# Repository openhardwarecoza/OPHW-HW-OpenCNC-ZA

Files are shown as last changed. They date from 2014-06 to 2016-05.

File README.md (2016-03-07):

# OPHW-HW-OpenCNC-ZA

Release link for Version 2: https://plus.google.com/+PetervanderWalt/posts/GEEHTLkx1Rs

Youtube Playlist: (Mostly the older V1 videos): https://www.youtube.com/watch?v=i0t9h2HhJ-g&list=PL1JTb6-HQgOwBOFXhe4r-cTgKN7O4TTUV
(Note: The V2 is a much more rigit beast than the V1 was - switching to OpenBuilds V-Slot made a massive difference over 12mm stainless shafts that V1 used)

Photos of the machines: https://github.com/openhardwarecoza/OPHW-HW-OpenCNC-ZA/tree/master/Photos

###Groupbuy of V2 Frames 

(March 2016:  $300 if we get 10 people): https://plus.google.com/112804366993013346159/posts/UJpufFbkruB

## New Version: V2
OPHW-HW-OpenCNC-SMW
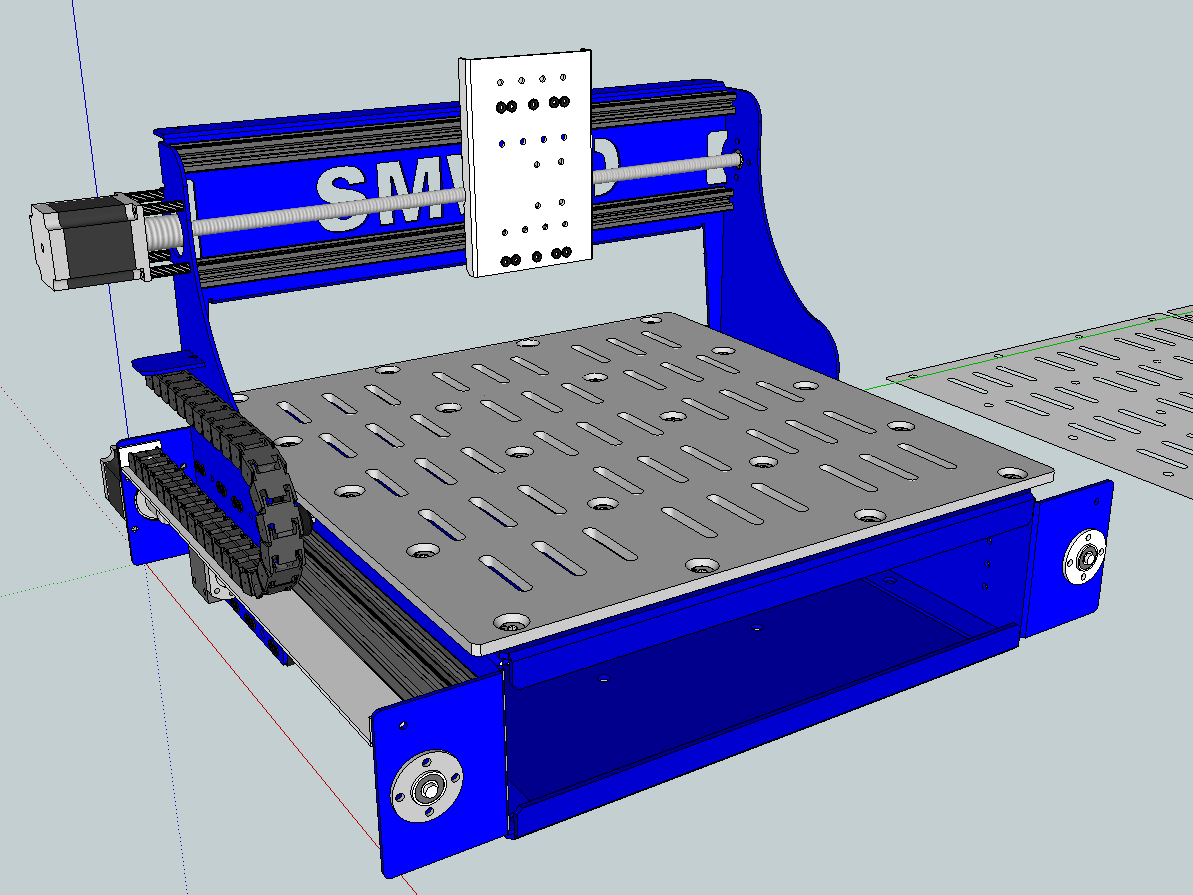
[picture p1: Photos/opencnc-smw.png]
OpenCNC-SMW


## Legacy Version:  V1
OPHW-HW-OpenCNC-ZA
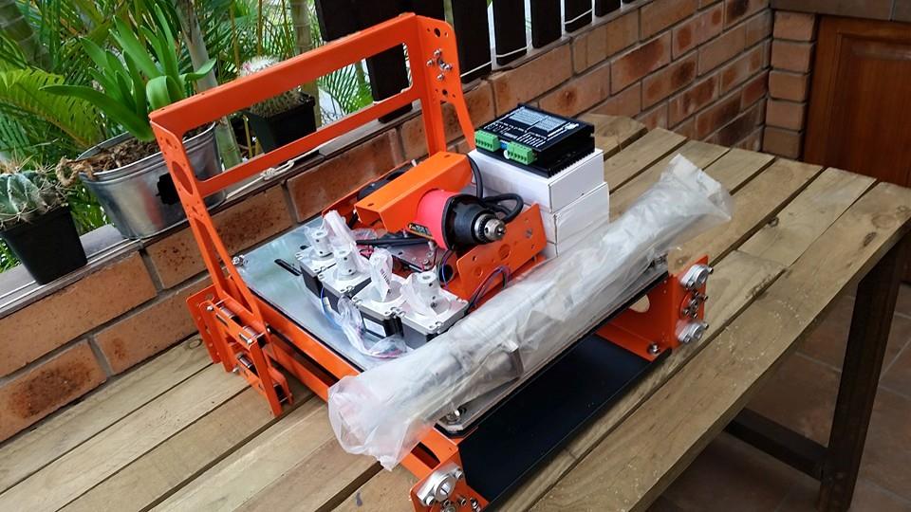
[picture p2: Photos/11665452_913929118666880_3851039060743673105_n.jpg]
OpenCNC-ZA


74 x Photos build Album of V1: https://plus.google.com/+PetervanderWalt/posts/8sR3STWhrXN

Specs V1: 200x300mm work area, 12mm ballscrews all round, 12mm stainless steel shafts,

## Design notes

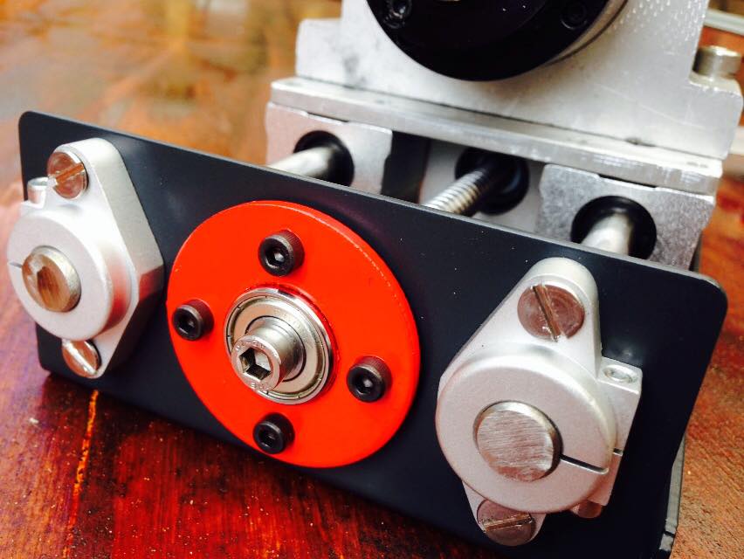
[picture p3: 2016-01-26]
Photos/10593230_783649345028192_9119679206650763691_n.jpg

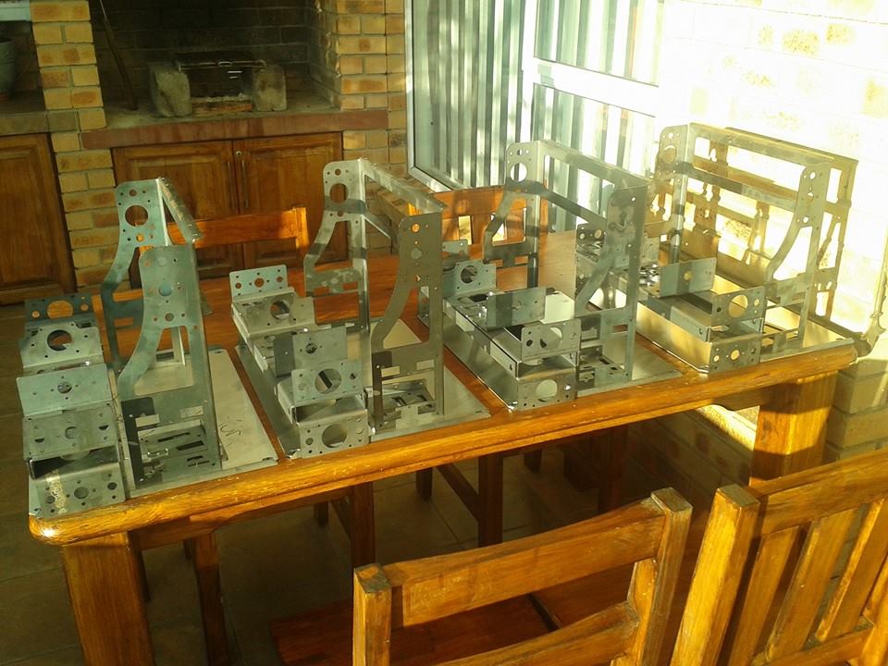
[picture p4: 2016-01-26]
Photos/537115_678176878908773_2035238081_n.jpg

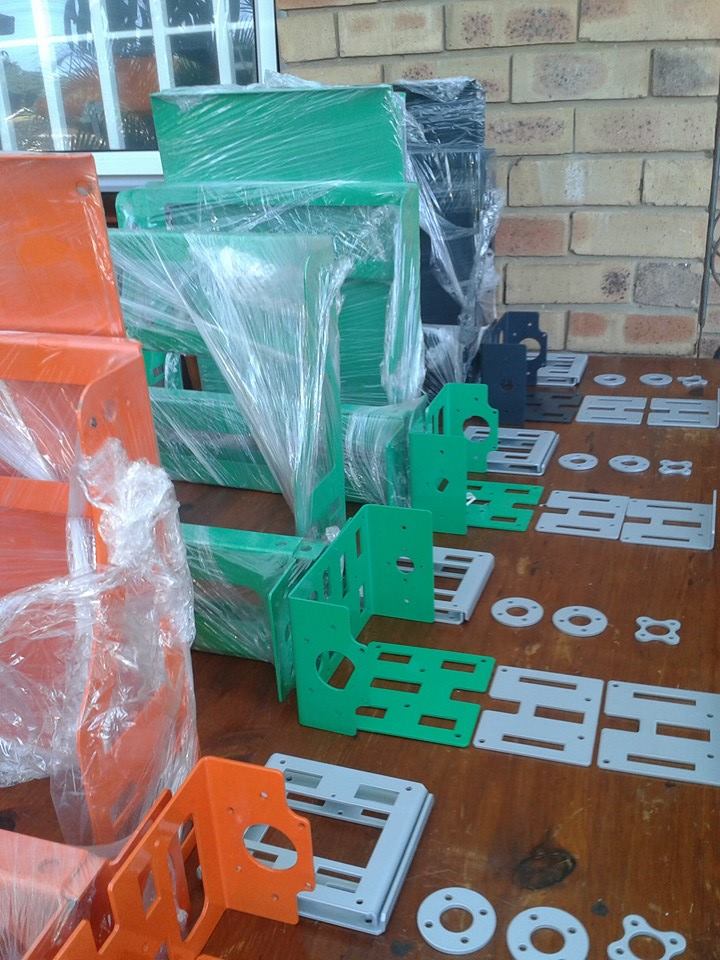
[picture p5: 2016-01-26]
Photos/10007480_681862631873531_1897662941_n.jpg

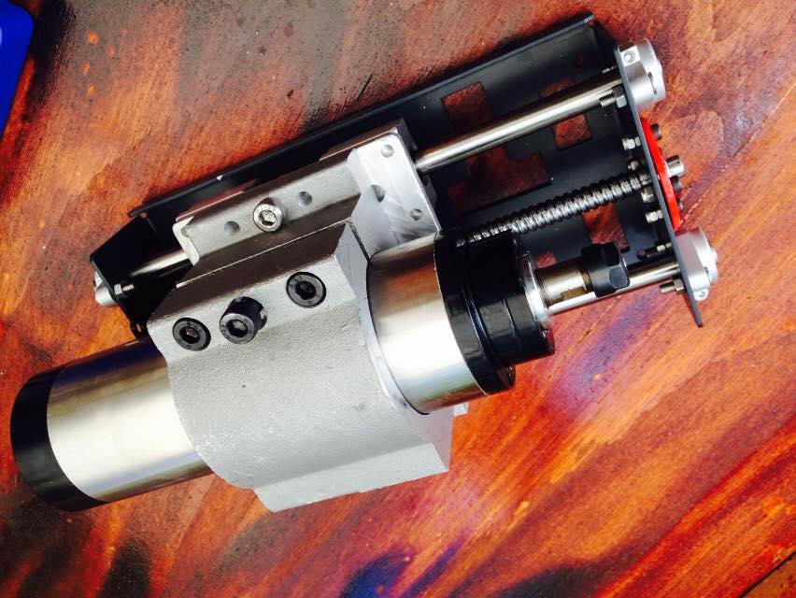
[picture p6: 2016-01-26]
Photos/10730114_783649301694863_8155415779819512405_n.jpg

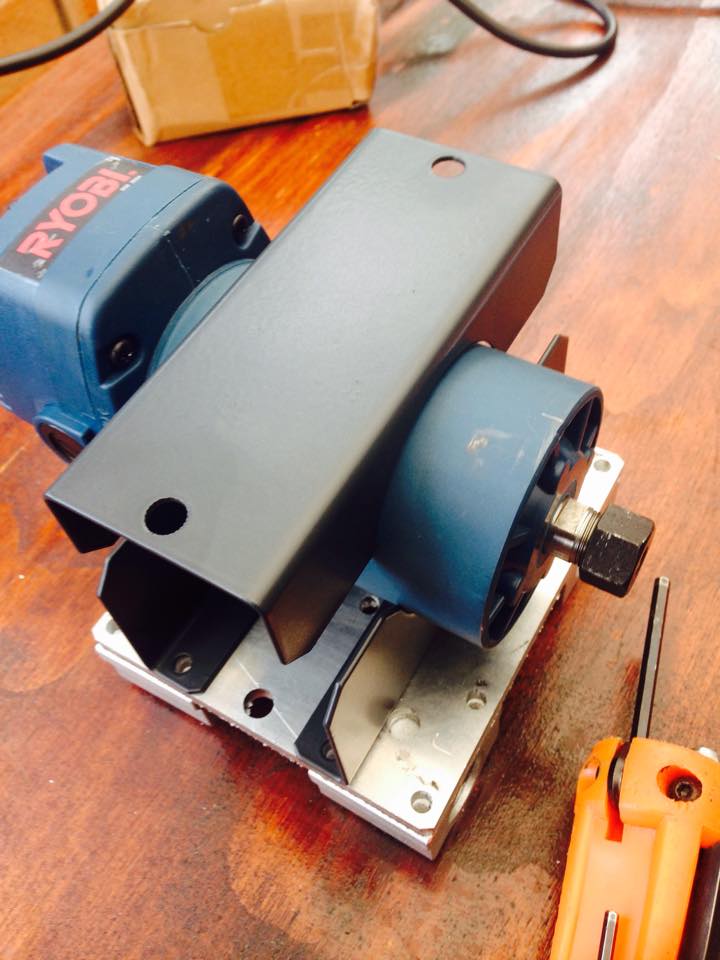
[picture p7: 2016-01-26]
Photos/1622716_788742607852199_260670169807607488_n.jpg

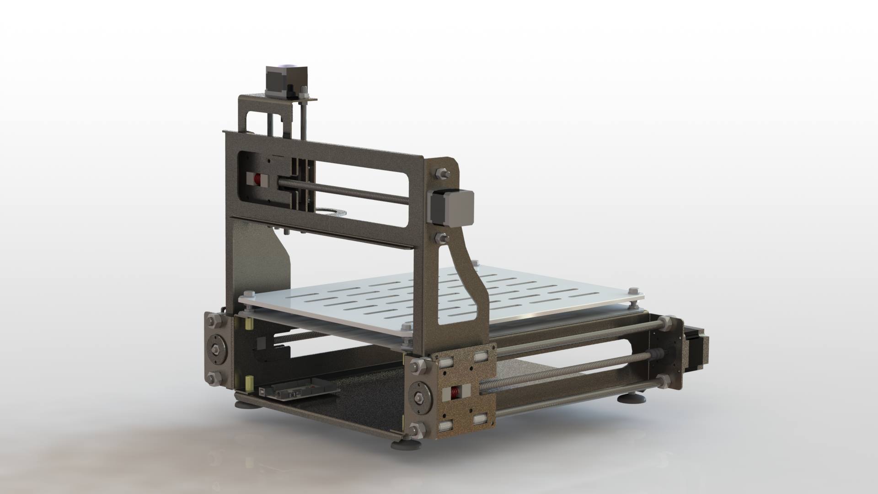
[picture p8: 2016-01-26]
Photos/1798963_653309631395498_944965548_o.jpg

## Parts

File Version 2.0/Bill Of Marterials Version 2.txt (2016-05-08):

(From OpenBuilds)
2 qty 20x80 VSLOT 500mm Length (Y Rails)
2 qty 20x20 VSLOT Between 500 and 530mm long - not critical (X Rails)
10 qty Openbuilds Spacer Blocks (http://openbuildspartstore.com/spacer-block/)
22 qty  OpenBuilds V-Wheels (Extreme PC would be even stiffer) http://openbuildspartstore.com/solid-v-wheel-kit/
11 qty 1/4 Eccentric Spacers http://openbuildspartstore.com/eccentric-spacer/
11 qty 1/4 Aluminum Spacers http://openbuildspartstore.com/aluminum-spacers/
12 qty 35mm Aluminum Spacers (Space motors out so couplers doesnt interfere inside moveable area of carriages) http://openbuildspartstore.com/aluminum-spacers/

(Z Axis)
1 x complete C-Beam Kit 250mm (Or own design) for openbuilds

(Leadscrews) (Note discussion on length on google plus)
3 qty 1204 Ballnut
3 qty 1204 Ballnut Mounting Block (like http://s.click.aliexpress.com/e/QvznIYRvZ)
2 qty Ballscrew 505mm between insides (So total length = 505mm + turned down section for shaft coupler + turned down and threaded section for restraining)
1 qty Ballscrew 530mm between insides  (So total length = 530mm + turned down section for shaft coupler + turned down and threaded section for restraining) 

Bolts and Nuts and Screws:
(Clamp Bed)
10 qty x Countersink Capscrew:  M8x30mm (Side rows - also clamps on sides)
10 qty x Countersink Capscrew:  M8x25mm  (two middle rows torsion box)
40 qty x M8 Nut (one between clamp bed and one below base top)
(NB Note: If you want to space the two by more than one nut height - account for it with spacers of some sort + extra longer bolts)

(Base bottom)
10 qty x Capscrew: M8x16mm (hold base plate to sides on bottom)

(Sides)
40 qty x M5 T Nut Drop In 
40 qty x M5 Capscrew (8 or 10mm long - to pass through the side and into the drop T nut to hold 8020 to sides)
8 qty x M5 x 16mm capscrews (for F608Z Clamp Plates)
8 qty x Nyloc M5 Nut (for F608Z Clamp Plates)
2 qty x F608ZZ Bearing  (or other ballscrew retention design)
2 qty x Shaft Coupler (6.35mm -> 8mm for as designed or better X type) (for example http://s.click.aliexpress.com/e/QR3BQ7q3v)
8 qty x M5 x 50mm capscrew  (to hold motor onto side)
8 qty x M5 Nyloc Nut (to hold motor onto side)

(Gantry)
12 qty x M5 T Nut Drop In 
12 qty x M5 Capscrew (8 or 10mm long - to pass through the side and into the drop T nut to hold 2020 to sides)
4 qty x M5 x 16mm capscrews (for F608Z Clamp Plate)
4 qty Nyloc M5 Nut (for F608Z Clamp Plate)
1 qty F608ZZ Bearing  (or other ballscrew retention design)
1 qty Shaft Coupler (6.35mm -> 8mm for as designed or better X type) (for example http://s.click.aliexpress.com/e/QR3BQ7q3v)
4 qty x M5 x 50mm capscrew  (to hold motor)
4 qty x M5 Nyloc Nut (to hold motor)

(Cable Chain Tray)
4 qty x M5 x 16mm Capscrew (Y Cable Chain tray)
4 qty x M5 Nyloc Nut (Y Cable Chain tray)
1 qty M3 x 10mm (hold cable chain tab to gantry)
1 qty M3 Square Nut(hold cable chain tab to gantry)

(VWheels)
22 qty x M5 x40mm bolts with flat head (like the ones sold by Openbuilds) for the VWheels

(Ballnut mounts)
12 qty x  5x 12mm capscrew (Mount ballnut blocks to carriages)
18 qty x M4 x 16mm capscrew (Mount ballnut to block)  
3 qty x M6 x 14mm Capscrew for threading into ends of ballscrew)

(Cable Chains) 
+- 3 meter of cable chain:  25mm wide

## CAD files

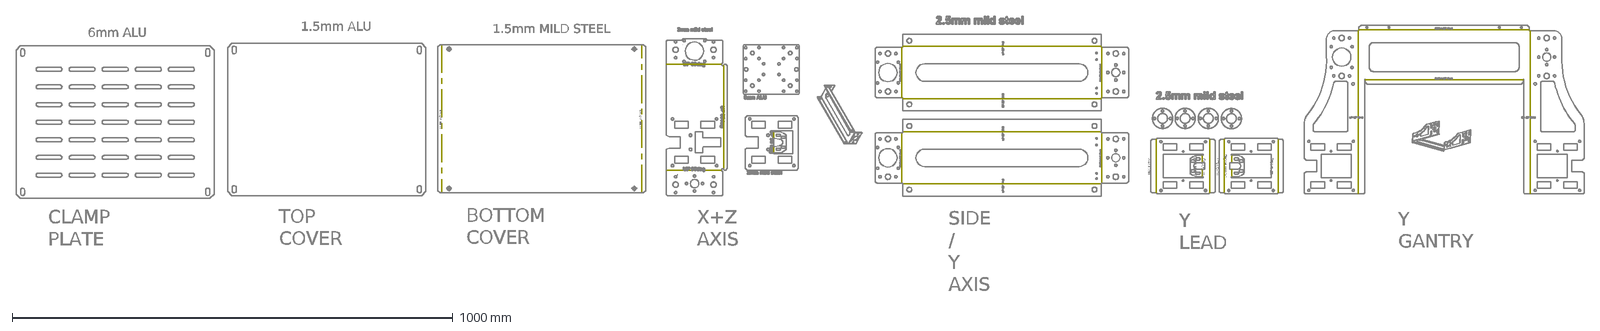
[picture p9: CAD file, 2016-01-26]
Production Ready DXF/opencncza.dxf
1.5mm ALU
DOWN 90Â° R 2
1.5mm MILD STEEL
6mm ALU
DOWN 90deg
UP 90deg
CLAMP PLATE
TOP COVER
BOTTOM COVER
X+Z AXIS
SIDE / Y AXIS
Y LEAD
Y GANTRY

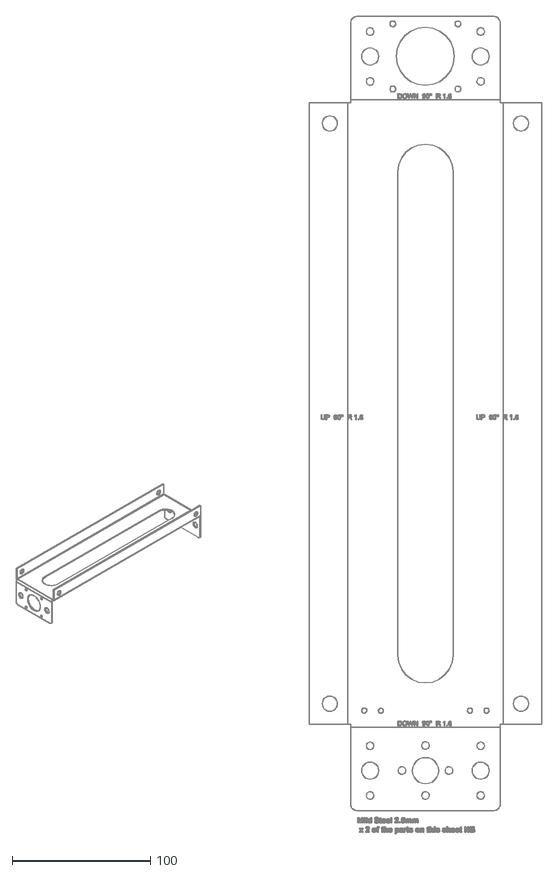
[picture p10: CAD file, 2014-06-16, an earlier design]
OLD/CNC-01-1100-01B Base left.dxf
380.4 x 591.5

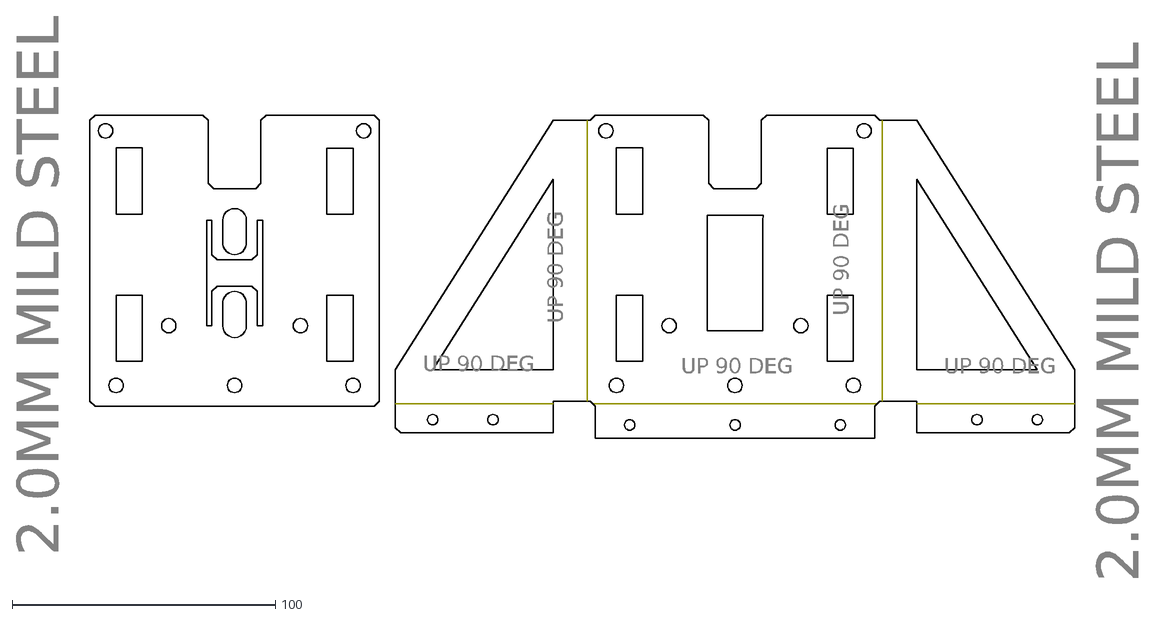
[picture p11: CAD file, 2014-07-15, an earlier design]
OLD/Orders/CNC-01-1200-Z-AXIS-M8.DXF
UP 90 DEG
2.0MM MILD STEEL

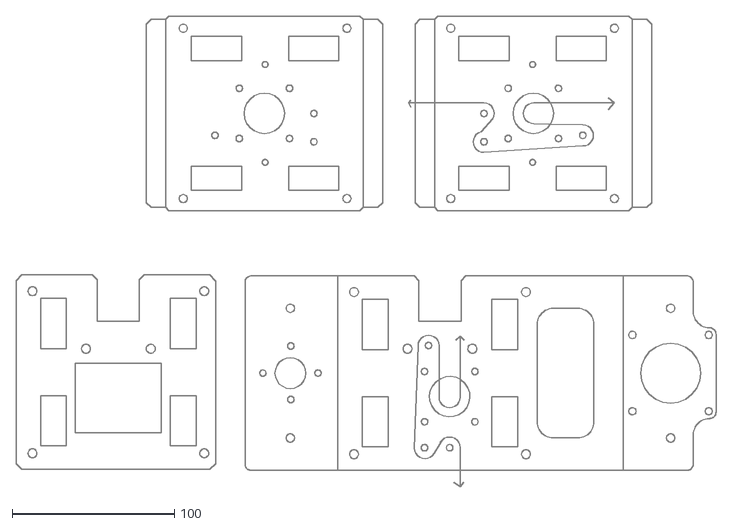
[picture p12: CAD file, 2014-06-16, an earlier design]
OLD/Belt Drive Test XY.dxf
431.8 x 290.4

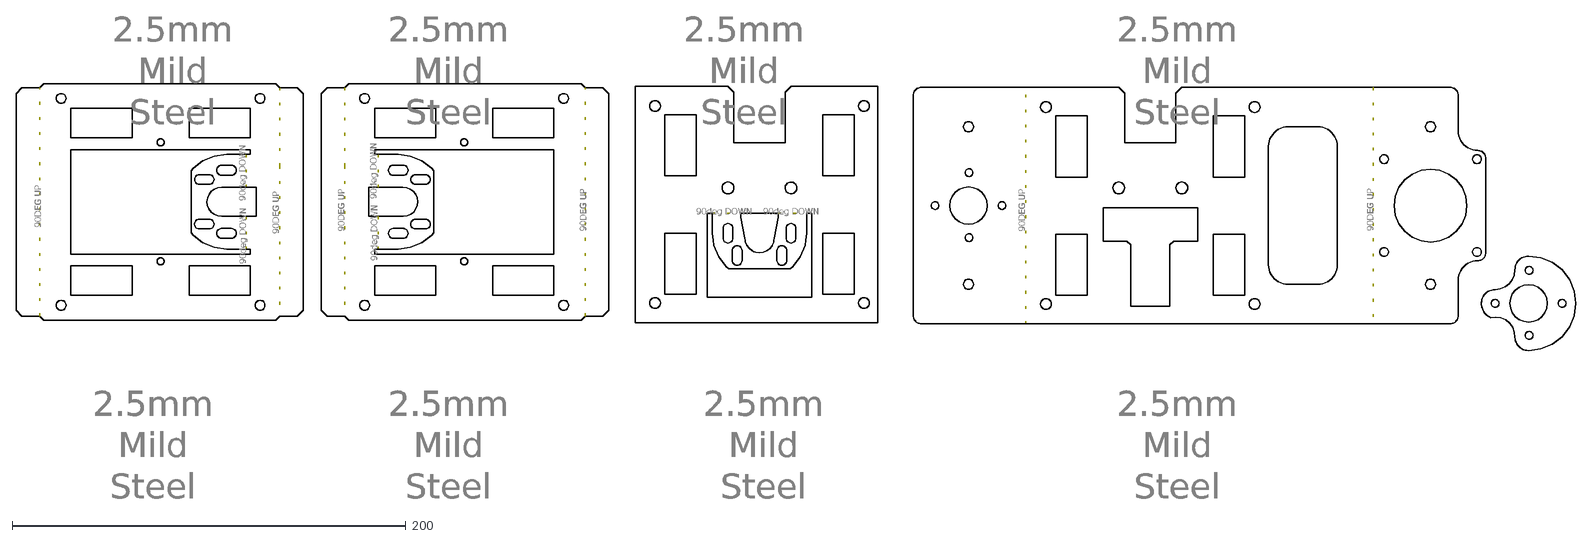
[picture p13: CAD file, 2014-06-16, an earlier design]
OLD/BallNut Mounts Side.dxf
90DEG UP
90deg DOWN
2.5mm Mild Steel

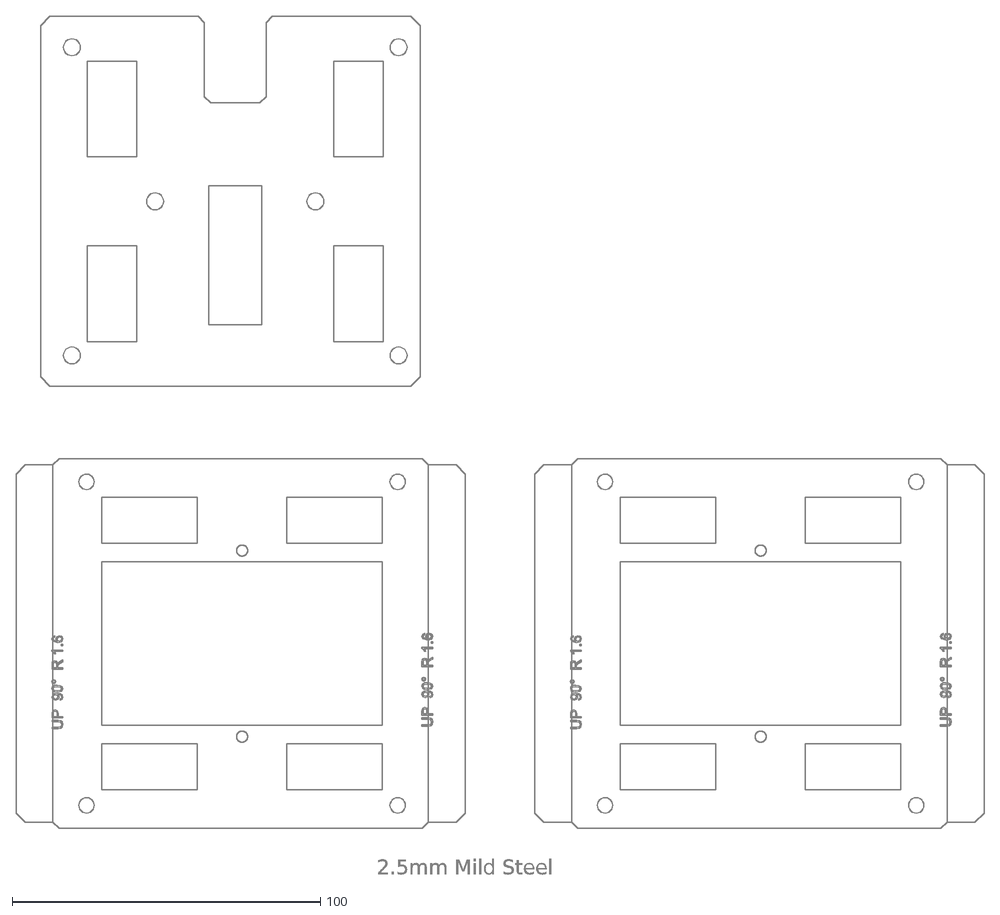
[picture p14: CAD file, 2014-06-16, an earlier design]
OLD/CNC-01-1000-03A Linear Bearing Holders.dxf
2.5mm Mild Steel

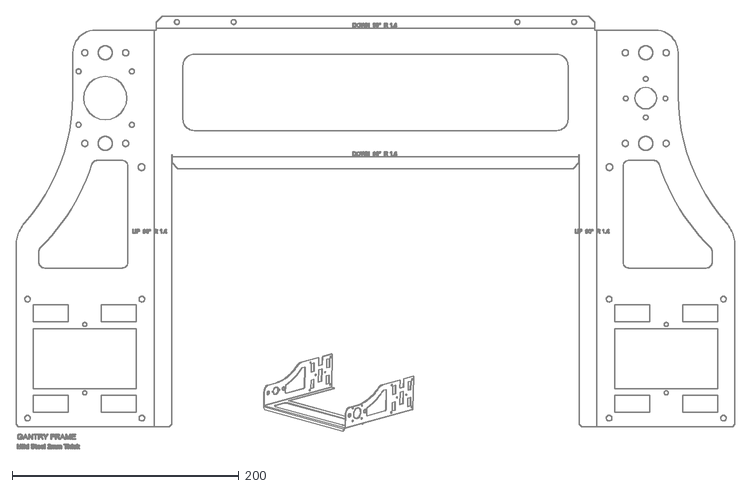
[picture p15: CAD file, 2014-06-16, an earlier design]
OLD/CNC-01-2000-01B_Beta Gantry.dxf
634.3 x 381.6

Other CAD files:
Version 2.0/DXF for Beta Run/OpenCNC-SMW3D untested beta.dxf
OLD/OpenCNC Complete.dxf
OLD/Orders/Hacker-Base and Gantry.dxf
OLD/Orders/CNC-01-1000-01A Clamp Plate.dxf
OLD/Orders/Pro-Base and Gantry.dxf
OLD/Orders/CNC-01-1100-04A Bottom.dxf
OLD/CNC-01-1100-04A Bottom.dxf
OLD/Orders/CNC-01-1000-02A Top Cover.dxf
OLD/CNC-01-3000-03B.dxf
OLD/CNC-01-3000-01B Tool Bracket.dxf
OLD/CNC-01-3000-02B Z Axis.dxf
OLD/1204 ballnut.skp
OLD/BallScrew Machining.skp
OLD/BallScrew2_BETA.dxf
OLD/BaseMods.skp
OLD/BearingMounts.skp
OLD/Belt Drive Test.skp
OLD/CNC-01-1000-01A Clamp Plate.dxf
OLD/CNC-01-1000-02A Top Cover.dxf
OLD/CNC-01-1000-03A BearingMounts.dxf
OLD/Gantry-Beta-V1.skp
OLD/Gantry-Beta-V2.skp
OLD/Open CNC - Beta 1204 Ballnut Mount Sides.dxf
OLD/Tool Bracket V2.skp
OLD/ZAxis-Ballscrew-Beta.skp
OLD/z-nut.stl
Version 2.0/Leadscrew Machining.skp

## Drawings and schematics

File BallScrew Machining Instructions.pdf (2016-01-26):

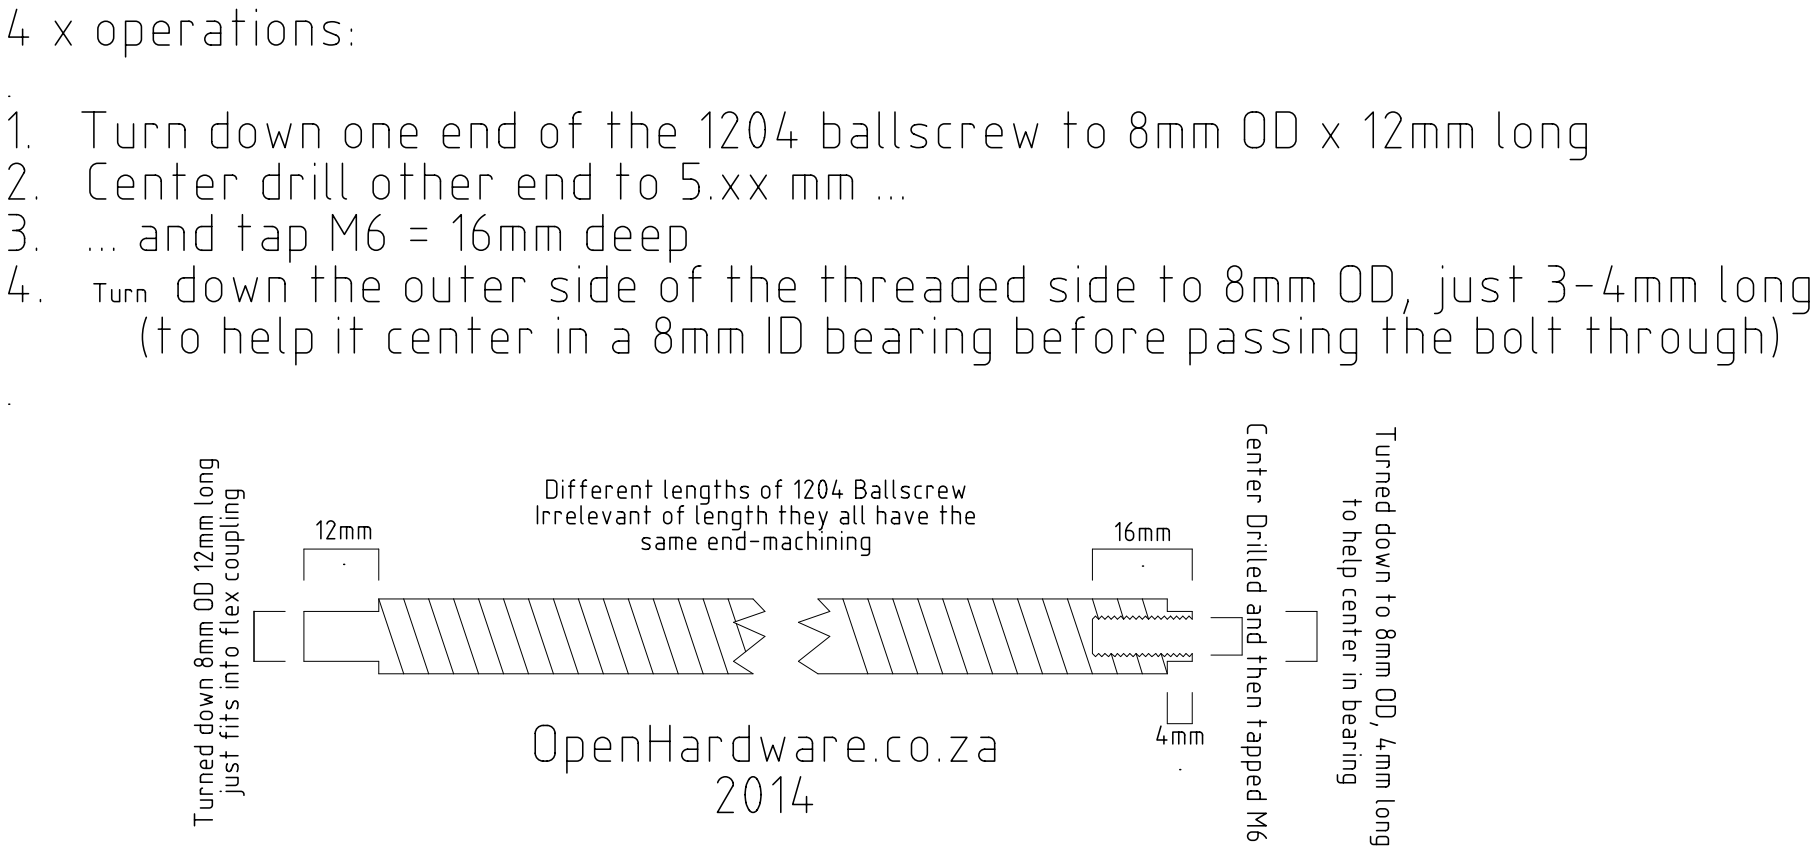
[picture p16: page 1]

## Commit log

2014-06-16 First commit of Mechanical and Electronic
    [1204 ballnut.skp, BallNut Mounts Side.dxf, BallScrew Machining.skp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]
2014-07-03 Changed the dimensions of some parts after beta
    Fixed some spacing issues we had during BETA1
    [CNC-01-1000-01A Clamp Plate.dxf, CNC-01-1000-02A Top Cover.dxf, CNC-01-1100-04A Bottom.dxf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]
2014-07-15 Added Stepper Driver
    [CNC-01-1200-Z-AXIS-M8.DXF, GrblControllerPi.brd, GrblControllerPi.sch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]
2014-07-28 Minor Tweaks to hardware + Added GrblpiB+ boards
    [Belt Drive Test.skp, GrblControllerPi.brd, GrblControllerPi.sch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]
2014-08-15 Added GrblPi Industrial
    [GrblPi B+Industrial.GBL, GrblPi B+Industrial.GBO, GrblPi B+Industrial.GBP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]
2014-08-15 Industrial Version: Gerbers as ordered
    [GrblPi B+Industrial.TXT, GrblPi B+Industrial.brd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]
2015-05-28 Single sided for Nicholas
    [GrblPiArgentina.brd, GrblPiArgentina.sch]
2016-01-26 Added Photos
    [1204 ballnut.skp, BallNut Mounts Side.dxf, BallScrew Machining.skp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]
2016-01-26 Cleaned up
    [1204 ballnut.skp, BallNut Mounts Side.dxf, BallScrew Machining.skp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]
2016-01-26 Added Ballscrew Instructions
2016-01-26 Added BOM
2016-02-03 Torsion Clamp Plate, fixed X idler mount, removed C-Beam Z Axis
2016-02-20 DXF for Samer
    [OpenCNC-SMW3D untested beta.dxf]
2016-05-08 BOM, Ballscrew sketch, and update drawing of CNC with spacers
    [Leadscrew Machining.skp]
